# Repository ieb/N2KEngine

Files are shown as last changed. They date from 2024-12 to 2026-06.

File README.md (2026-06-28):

# N2K Engine Monitor

This monitors an engine, mostly temperatures and fuel, emitting suitable N2K messages. Targeting a Volvo Penta D2-40. Code and pcb are based on the interface board in https://github.com/ieb/EngineManagement, however this time the pcb is from scratch using a Atmel 328p directly to make the unit more robust. The original has been in service for 3 years with no problems seen, outlasting the Volvo Penta MDI unit, which failed 2x in < 4 years. Ok, the replacement was based on relays following the Perkins schematic for the same engine, so not really hard to do.

# PCB

Single board. If using a 328p chip you will need to flash the bootloader. See programBootLoader for details. 

## 328p based board 

<div>
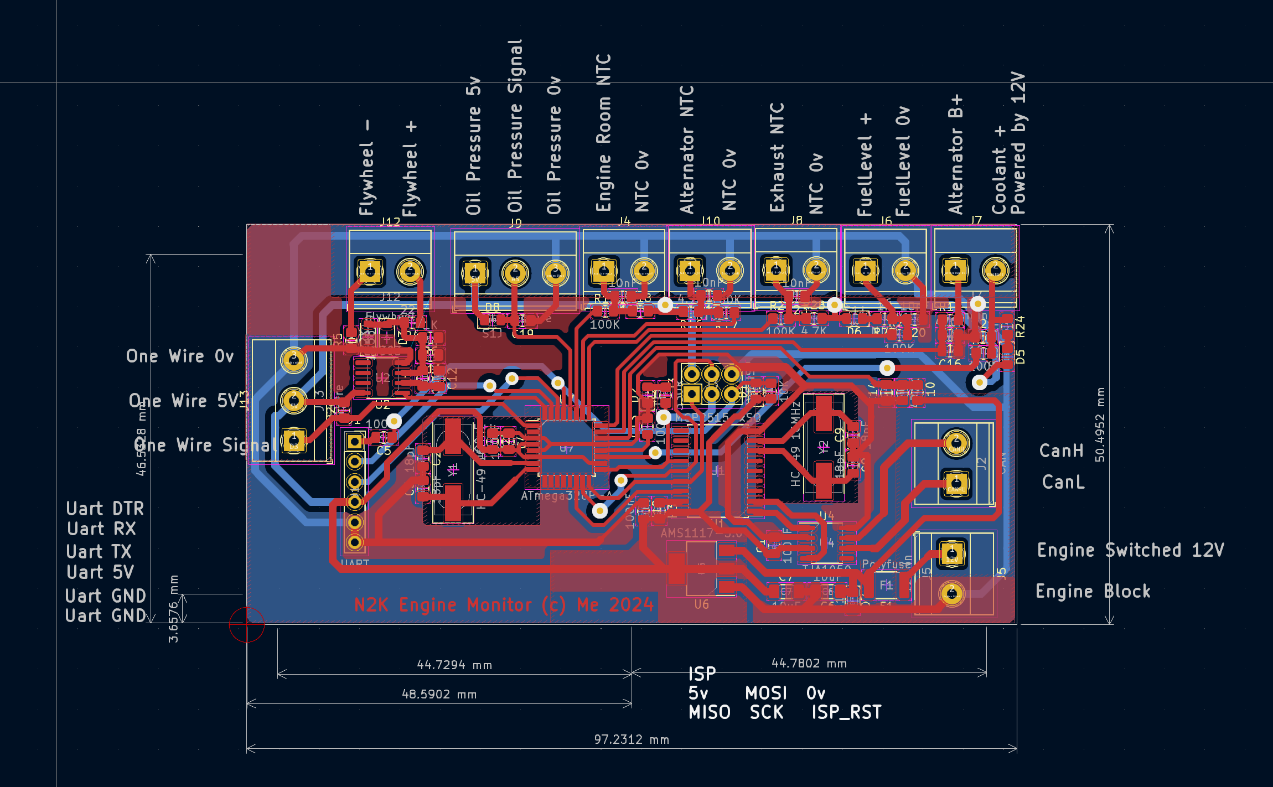
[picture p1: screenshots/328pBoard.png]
board

</div>

## Attiny3226 Board, 12bit ADCs and better RPM accuracy

<div>
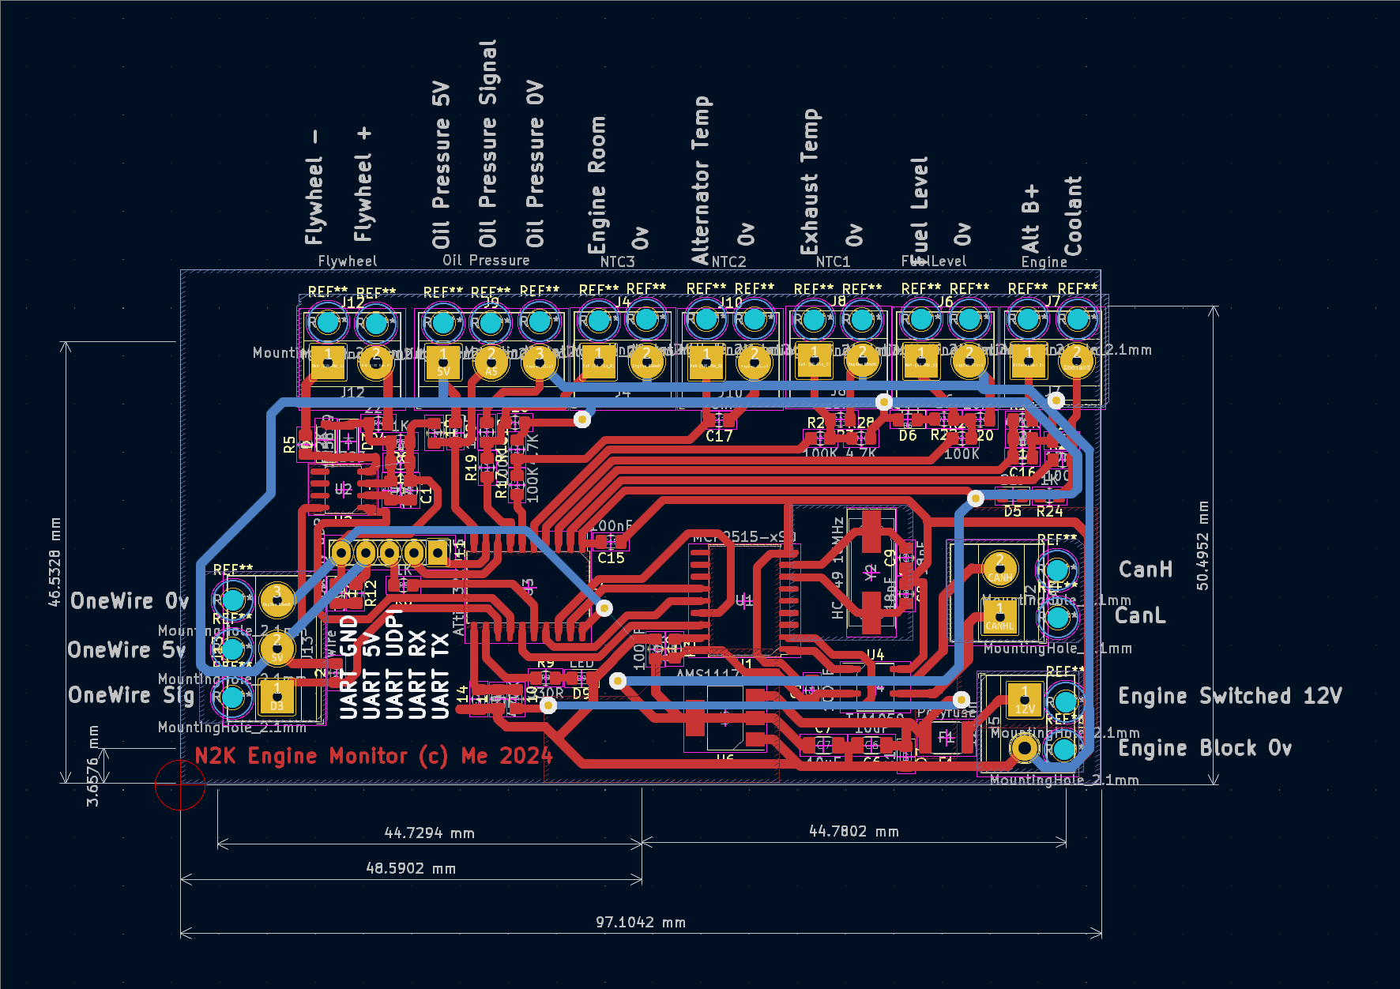
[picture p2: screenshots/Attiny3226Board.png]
board

</div>

# Setup

Setup starting with a new board, this is for 3226 which the preferred board.

* Test the board supply to check power consumption, should be about 30mA at both 5v and 12v.
* Connect up a UDPI programmer, and serial monitor.
* Burn Fuses, and tune the internal clock on the 3226, see tuning3226/README.md
* Upload the code.
* Connect a CAN bus with 1 other device.
* Verify CAN messages are sent and received (menu item d)
* Measure and set the supply voltage to the chip after powering with 12v. (menu item V)
* Check the Sensor diagnostics (menu item D, and M), might need to connect some NTC sensors and fake up flywheel source.
* Set the engine hours to match the existing board.
* Install the board

## Connection notes

* The GND connection must be made to the engine block (star pattern) to avoid GND voltage differences when the anternator is charging. Do not GND on the battery as that will result in dips in the coolant temperature of 5C or more. The battery voltage will include the GND drop on the charging line.

* The exhaust NCT should be connected to a part of the wet exhaust with good thermal connection to the inside of the exhaust. Do not connect to the elbow on the engine as this could result in false alarms when starting a warm engine. The trigger level is 45C or an 8C every 30s rise. Typically an exaust in UK waters on a D2-40 rests at 34-37C and rises rapidly should raw water fail.

## Changes from original build 4 years ago

* All components SMD, no draughtboards or modules with pin headers to fail.
* Switched from a LM385 to a LMV393 for the flywheel pulse generator as all I need is a clean square wave to count the pulses. (actually I miss ordered 10 LMV393's and then switched over).
* Changed to a 16MHz crystal on the MCP2515 since this is what the 328p is using. Perhaps 1 crystal would work for both, but probably not.

# Memory usage

after reducing memory requirements (580 used before), varies up an down a bit with debug.

attiny3226

    RAM:   [==        ]  20.1% (used 619 bytes from 3072 bytes)
    Flash: [========  ]  81.1% (used 26579 bytes from 32768 bytes)
NB, no malloc in use in code.
Over 77% Flash usag pio inspect no longer works, however removing One wire code may give enough space for debug symbols to allow inspect to work

# Status bits.

The status bits in PGN 127489 are set to indicate an alarm condition.

Alarm set levels and alarm clear levels are in enginesensors.h

WHen an alarm condition is set if the check engine, maintenance or emergency stop bits are set, they are not
cleared when the alarm clears. Generally advisable to stop the engine and check.

Emergency stop will be set when temperatures are too high. Best to stop the engine before damage occurs.

Over Temperature status 1 bit 1 set when over temperature is suspected including coolant (> 97C), exhaust > 45C, alternator > 110C, engine room > 70C. Will also set check engine and engine emergency shutdown alarms.

Low oil pressure alarm is set when oil pressure is < 10psi.

If sensors fail then engine comms alarm is set.

Water flow alarm uses the wet exhaust silencer probe as a proxy for raw water flow. The probe is mounted on the silencer body, which is in direct contact with the wet exhaust but thermally isolated from the engine block and heat exchanger — so silencer temperature reflects exhaust gas vs raw water flow only, and is not biased by block temperature on a warm restart. Two independent triggers, both gated on engine running, past the start-up grace period, and not stopping:

* Absolute over-temp: exhaust > 45C. WATER_FLOW and CHECK_ENGINE are set on the first sample; EMERGENCY_STOP is held off until the condition has persisted for 5s so a single noisy ADC sample cannot trip it.
* Rate-of-rise: exhaust climbs more than 8C in any 30s window once past the 35C baseline. This catches a flow failure before the absolute threshold (the 21-Jun-2026 incident showed a +9C rise in the first 30s while still well below 45C).

A coolant-vs-exhaust convergence check was previously included but removed: on a warm restart the silencer takes several minutes to thermalize while coolant is already at operating temperature, producing a coolant–exhaust gap that approaches the trip margin under entirely healthy conditions.

The alarm clears only once exhaust drops below 38C (widened from 40C) to avoid chatter on a cooling elbow.

Charge indicator alarm is set when the alternator voltage is < 12.8V

Engine shutdown alarm will be set when the engine is shutting down.

Other alarms are not set at this time.

# Building and Uploading

## Attiny3226 based board

Use UDPI. I use the old, slow and slightly buggy jtag2udpi programmer loaded onto an Uno. I use https://github.com/ieb/jtag2updi forked just in case. After programming the Uno needs a 10uF cap between reset and ground to prevent a reset on the Uno when programming starts.  The UDPI output is on Digital Pin 6 and connects via a 4K7 Resistor to the UDPI pin on the Attiny3226. The target board should be powered separately, and the serial monitor can remain attached while programming. Do not power the board using both a serial converter and the 12v power supply as this will cause the serial port to draw too much USB current and be shutdown. Programing setup is in platformio.ini. Before programming a fresh chip, set the fuses to set the CPU Frequency.

Fresh boards also need to go through a runing process , see tuning3226/

Obviously edit platform.ini with the correct serial ports for upload and monitoring.

    pio run -e attiny3226 -t fuses

Then upload code with an upload command. Fuses only need to be set once per chip.

    pio run -e attiny3226 -t upload

To monitor 

    pio device monitor

### Clock Tuning 3226

The 3226 board uses an internal oscilator due to lack of pins and so it needs tuning from a board with a quartz crystal as per https://github.com/SpenceKonde/megaTinyCore/blob/master/megaavr/extras/Ref_Tuning.md. The Tuning source needs to be https://github.com/SpenceKonde/megaTinyCore/tree/master/megaavr/libraries/megaTinyCore/examples/TuningSource uploaded onto a Uno or any 328p with pin 9 available. The UNO must have an real crystal not a resonator.  The tuning code is https://github.com/SpenceKonde/megaTinyCore/tree/master/megaavr/libraries/megaTinyCore/examples/megaTinyTuner, but for these boards must be modified to use PB1 as the timing pin since this is exposed directly. (Oil pressure sense).  Copies of both of these are in tuning as they needed minor modifications.

## 328p based board

Can be built on any 328p suitably wired, however to build using the pcb design first flash a bootloader, see [programBootLoader/README.md] for details, then come back here.

Having flashed with the urbootloader connect a serial adapter configured for 5V to the serial header pins, adjust platform.ini to reflect the serial port and run

    pio run -t upload

to monitor

    pio device monitor

Do not attempt to power the board both on the 12v line and through the serial port 5v at the same time. This will probably shutdown the USB port on your laptop (or worse produce some smoke) Monitoring over serial can be done provided only GND, TX and RX are attached. Ie no power from the serial adapter.

# LM393 RPM to pulses

Critical that this chip as a 100nF decoupling capacitor. Without it it will generate pulses from power supply noise with the inputs shorted together. See schematic. LTSpice models don't predict this behavior.

# Engine Events

Stores upto 29 events in EEPROM, with a 15s resolution and one of upto 255 types.
All the following PGNS have standard priorietary PGN format + a Function code byte.
The Manufactore code is 2046 and the Industry is Marine, ie 4.

# PGN Abuse

Since Raymarine instuments display only a asubset of PGNs, some are beeing abused to get critical temperatures avialable on the insturments.

* alternator temperature, critical for LiFePO4 charging, is sent as oil temperature in Dynamic Engine Parameters (PGN 127489)
* ehxhaust temperature, critical for raw water flow monitoring, is sent as transmission oil temperature in Dynamic Transmiossion Parameters (PGN 127493L)

# Temperature PGN 130312 non standard IDs

* Exhaust temperature is sent as ID 30
* Additional OneWire Temperature probes are sent as IDs 31-35 where present.

## PGN 65305L

Standard  Packet proprietary, 8 bytes

| Field | Length | Value     | Description            |
|-----------------------------------------------------|
| 1     | 11 bits| 2046      | Manufacturer code      |
| 2     | 2 bits |           | Rserved                |
| 3     | 3 bits | 4 (0b100) | Industry Code          |
| 4     | 8 bits |           | Requst Function Number |
| 5     | 5 bytes|           | reserved/payload       |

|  Function | Description | Valid PGN | Response |
|---|---|---|---|
| 11 | Get events | 65305L | Events PGN 130817L Functon 12 |
| 12 | Get events response | 130817L | List of events |
| 13 | Clear events | 65305L | ACK PGN 65305L Functon 14, no payload |
| 14 | Clear events ACK | 65305L | Ack clear events, no payload |

## PGN 130817L

| Field | Length | Value | Description |
|---|---|---|---|
| 1 | 11 bits| 2046 | Manufacturer code |
| 2 | 2 bits | | Rserved |
| 3 | 3 bits | 4 (0b100) | Industry Code |
| 4 | 8 bits | | Requst Function Number |

## Function 12

| Field | Length  | Value | Description | 
|---|---|---|---|
| 4 | 1 byte  | uint8_t | Number of events |
| 5+(n*4) | 1 byte  | uint8_t | Event ID |
| 6+(n*4) | 3 bytes | 3Byte UDouble 0.001 | Engine Hours of event (15s resolution) |

| Event ID | Meaning |
|---|---|
| 0 | Current engine hours, no event |
| 1 | Engine Stop |
| 2 | Low Oil Pressure |
| 3 | High Coolant Temperature |
| 4 | High Exhaust Temperature |
| 5 | High Alternator Temperature |
| 6 | High Engine Room Temperature |

# Todo

* [x] build board.
* [x] Flash bootloader and test
* [x] Port code from original
* [x] Allow for 16MHz MCP2515 oscillator, current library uses 8MHz.
* [x] Handle when engine not running, now that device is powered from CanBus
* [x] Reduce memory requirements in EngineSensorts and bind measurements to messages.
* [x] PR SmallNMEA2000 with changes
* [x] Test and Calibrate NTCs
* [x] Test and Calibrate Coolant and fuel
* [x] Test On N2K Bus
* [x] Implement 1 wire
* [x] Allow Engine Hours to be set via serial
* [x] Improve status and diagnostics to include n2k traffic
* [x] Implement status alarms
* [x] Consider swapping NTC4 for a oil pressure sensor if it can be accommodated.
* [x] Power from Engine supply since oil pressure sensors use > 10mA typically. This means fuel levels and temperature will only be available with engine controls turned on.
* [x] Check voltage calibration, some doubt over digtal multi meter accuracy used previously - verified against a ADS1115 to be accurate
* [x] Add firmware version, shows on the help, press h when connected over serial.
* [x] Create a attiny3226 based board, with 12bit ADCs for better resolution on the voltages.
* [x] Calibrate CPU clock
* [x] Verify RPM accuracy (measured at +- 0.2% relative to calibrated 16Mhz crystal)
* [x] Verify NTC and other ADC readings.
* [x] Install onboard
* [x] Implement event storage
* [x] Implement PGN proprietary messages to query engine events.
* [x] Update schematic to improve ADC stability when charging main LiFePO4s
* [x] Fix OneWire on Attiny3226 (see lib/vportonewire)
* [x] Fix event streaming to contain the right number of events including current hours.
* [x] Read stop button, on PC0. This will go to 12V when the solenois is powered.
* [x] Lowered alternator low voltage alarm to 12.2v and added window for overheat to combat high noise levels on the coolant sensor.
* [x] Added window period for all alarms to avoid 1 reading triggering alarm condition, set a 5s. 
* [x] Fixed (hopefully, need to test on engine) noise in in Engine Coolant readings, due to 12v ripple.
* [ ] Check the divders, which we specked at 100K/47K which could be too large for the ADC capacitance.

# Could do... but probably will not

The board currently runs of switched engine power, so to read fuel tank and batteries the engine has to be turned on. This is good, since power consumption becomes irrelevant although its typically < 80mA. I could optimize so that the board could be powered from the Can bus, but probably wont. Better to have it off when 
not relevant.. eg when sailing.

# New Board check list

* Oil sensor with pot
* NTCs, set Vdd then 10K == 25C, 22K == 8C, Check thermstor against room temp and body temp.
* Check Fuel 190R == full 0R == empty, linear, 120R == 120/190 = 63%  47/190 == 24
* Check AltV by connecting to suppy V
* Check Coolant, Supply -> 1K top. 22R == 120C, 120R == 60+10*(134-120)/(134-97) = 63
* Check RPM with a 1KHz signal
* Check oneWire
* Check CAN and engine events are responding, verifies can read and write.

# Engine overheat data from 21 July 2026.

Had been motoring for about 45m, 2.2K rpm all stable.

* 10:08:45 Coolant 87C, Exhaust 38.4C, Engine Room 57. raw water hose detaches, sudden drop in Engine Room temperature due to water spraying engine bay. Exhaust note changed.
* 10:09:00 Coolant 90C, Exhaust 40.2, Engine 50C
* 10:09:15 Coolant 92.7C, Exhaust 47.1, Engine 49.4C
* 10:09:30 Coolant 95.2C, Exhaust 51.9, Engine 48.6C  <<< Should have alarmed here.
* 10:09:45 Coolant 97.4C, Exhaust 57.9, Engine 47.3C
* 10:09:55 Coolant 98.3C, Exhaust 62.6, Engine 47.1C  engine was turned off before overheat.

Exhaust elbow temperature rises rapidly 22C over 1m vs 8C over the same period for the engine coolant temperature, although at the time no raw water alarm sounded as the limit was set at 80C and there was no display showing exhaust temperature.

Exhaust elbow temperature seems to be a strong indicator of water flow once the engine is running at temperature.

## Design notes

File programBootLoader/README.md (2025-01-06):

# Program an Arduino UNO with Arduino ISP 

Only the 328p based board needs a bootloader. The Attiny board is programmed over UDPI with no bootloader, see main readme.

This will program a 328p with a urboot bootloader from https://github.com/MCUdude/MiniCore where previously there was none. Once the bootloader is used, standard programming over UART can be used. Fuses are also set here, see platform.ini here for more details.

## Connect

* Uno 10uF between RST and GND to stop it reseting while programming
* Uno -> Target
* 0V -> 0V
* 5V -> 5V
* D10 -> ISP Reset
* D11 -> MOSI
* D12 -> MISO
* D13 -> SCK

run

    pio run -e fuses_bootloader_uno_isp -t bootloader

output should end with....

        ....
        avrdude: verifying ...
        avrdude: 1 bytes of lock verified

        avrdude: safemode: lfuse reads as F7
        avrdude: safemode: hfuse reads as D6
        avrdude: safemode: efuse reads as FC
        avrdude: safemode: Fuses OK (E:FC, H:D6, L:F7)

        avrdude done.  Thank you.

        =========================================================================== [SUCCESS] Took 3.98 seconds ===========================================================================

        Environment               Status    Duration
        ------------------------  --------  ------------
        fuses_bootloader_uno_isp  SUCCESS   00:00:03.983
        =========================================================================== 1 succeeded in 00:00:03.983 ===========================================================================

Then the LED on SCK should be flashing. The default program is blink.

Now the board can be programmed over UART as normal. The bootloader is urboot

# Errors

If avrdude reports

    avrdude: stk500_recv(): programmer is not responding

Then check the 10uF cap is connected properly (or the wrong port is used)

If avrdude reports

    avrdude: Device signature = 0x000000
    avrdude: Yikes!  Invalid device signature.
             Double check connections and try again, or use -F to override
             this check.

Try swapping MOSI and MISO

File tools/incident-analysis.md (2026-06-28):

# Engine cooling-failure analysis — May & June 2026 incidents

Analysis of two raw-water-flow / overheat events captured by the
`nmeabridgeapp` per-day binary history, used to validate the water-flow
alarm-logic changes in `lib/enginesensors/`.

Source data: `nmeabridgeapp/datasets/engine-YYYY-MM-DD.bin` (one record per
second, format documented in `nmeabridgeapp/doc/history-log-format.md` and
`EngineProtocol.kt`).

Decoder: `tools/engine_log.py` — pure-Python, stdlib only. Subcommands:

```
python3 tools/engine_log.py summary <files>           # per-run statistics
python3 tools/engine_log.py csv     <files>           # per-second CSV
python3 tools/engine_log.py trace   --peak coolant <files>   # window around peak
```

## Healthy baseline (D2-40, all good runs across 30–31 May, 20–21 Jun 2026)

| metric | typical warmed-up range |
|---|---|
| coolant | 80 – 92 C |
| **exhaust elbow** | **31 – 39 C** (mean 34–36 C) |
| coolant – exhaust gap (rpm > 1200) | **45 – 55 C** (means 48–52 C) |
| alternator | 60 – 85 C |
| engine room | 40 – 65 C |
| alternator V / battery V | 13.7–14.5 / 13.5–14.0 |

Confirms the firmware comment that "normal water flow on the elbow is 37C".
The alarm constants — 45 C absolute trip, 35 C rise-anchor baseline,
8 C rise-in-30 s — are all comfortably outside healthy variation.

## Why no coolant-convergence trigger

An earlier version of the firmware included a coolant-vs-exhaust convergence
trigger (fire if `coolant - exhaust < 30 C` once coolant > 70 C). It was
removed after the warm-restart sequence on run 2 of 21 Jun was inspected:
the silencer (where the exhaust probe is mounted) is thermally isolated from
the engine block, so on a warm restart the block is at ~85 C while the
silencer has cooled toward ambient. At 09:30:45 — engine at 1380 rpm, all
healthy — coolant was 82.0 C and exhaust 51.4 C: gap 30.6 C, **0.5 C from
tripping the convergence alarm**. Exhaust then fell monotonically for ~5 min
as raw water cooled the silencer faster than exhaust gas heated it, before
diverging into the normal ~50 C steady-state gap. Convergence is therefore
a false-positive risk on every warm restart, while contributing no
detectable lead time on either captured failure mode (it does not fire at
all on the sudden-detachment case and is the *last* of the three triggers
to fire on the slow-degradation case). Removed.

## Note on dating

The README incident headed *"21 July 2026"* is in fact recorded in
`engine-2026-06-21.bin` at 09:09 UTC (10:09 BST). There is no
`engine-2026-06-22.bin`. Both this document and the README's narrative
refer to the same 21 June 2026 event.

## Incident A — 2026-05-31, slow flow degradation

Run starts 10:03:35 UTC at ~1500 rpm, coolant ~62 C from a previous warmup.
The exhaust elbow climbs roughly linearly from start: about +1 C every
5 s once past 30 C, i.e. ~12 C/min — well above the new rate-of-rise
threshold (8 C in 30 s).

| time (UTC) | rpm | coolant | exhaust | gap | event |
|---|---|---|---|---|---|
| 10:03:44 | 1348 | 64.0 | 27.1 | 36.9 | start, gap normal |
| 10:04:34 | 1522 | 66.1 | 31.3 | 34.8 | exhaust climbing fast for a cold engine |
| 10:05:54 | 1664 | 79.6 | 45.7 | 33.9 | exhaust > 45 C — abs trip |
| 10:06:09 | 1675 | 78.7 | 50.5 | 28.2 | gap < 30 C — convergence trip |
| 10:07:39 | 1333 | 96.6 | 66.2 | 30.4 | coolant > 95 C |
| 10:08:39 | 1341 | 91.6 | 74.1 | **17.5** | gap collapsed |
| 10:09:11 | 1350 | **101.2** | 77.5 | 23.7 | peak coolant |
| 10:09:14 | 759 | 98.2 | 78.0 | 20.2 | rpm cut to idle |
| 10:09:24 | 767 | 99.1 | 78.4 | 20.7 | CHECK_ENGINE / MAINTENANCE asserted |
| 10:09:39 | 764 | 99.1 | 79.7 | 19.4 | OVERTEMP asserted |
| 10:09:54 | 769 | 100.7 | 80.0 | 20.7 | last sample, engine off shortly |

When the new alarm logic would trip (replayed against the data):

| trigger | first fires at | lead time vs OVERTEMP (10:09:39) |
|---|---|---|
| rate-of-rise (8 C / 30 s) | ~10:05:30 (cool 73 C) | **~4 min earlier** |
| absolute > 45 C | 10:05:54 (cool 80 C) | ~3 min 45 s earlier |

The old code (45 C absolute, no persistence) also tripped at 10:05:54, but
OVERTEMP was the only bit eventually set in the historical record — and
that didn't happen until 4 minutes later. **This is the failure mode where
the new rate-of-rise trigger adds real, measurable detection time.**

## Incident B — 2026-06-21, sudden hose detachment

Warm restart at 09:30 BST, stable cruise at ~2200 rpm. Coolant locks at
86–87 C, exhaust at 37–38 C, gap at ~49 C for ~9 minutes — textbook
healthy operation. Then a hose detachment causes the failure described in
README §"Engine overheat data from 21 July 2026" (date typo in README).

| time (UTC) | rpm | coolant | exhaust | gap | event |
|---|---|---|---|---|---|
| 09:08:45 | 2235 | 87.1 | 38.4 | 48.7 | normal |
| 09:09:00 | 2235 | 90.0 | 40.2 | 49.8 | hose detaches; exhaust climbing |
| 09:09:15 | 1480 | 92.7 | 47.1 | 45.6 | exhaust > 45 C; skipper throttles back |
| 09:09:30 | 1632 | 95.8 | 51.9 | 43.9 | coolant > 95 C |
| 09:09:45 | 1480 | 97.6 | 57.9 | 39.7 | — |
| 09:09:55 | 833 | 98.3 | 62.6 | 35.7 | engine going to idle / shutdown |
| 09:09:58 | 833 | — | 62.6 | — | coolant signal lost (engine off) |

Exhaust rose **+24 C in 55 s** (~26 C/min). No alarm bits were set by
the firmware in service that day — the only status1/2 flag seen on 21 Jun
across the whole file was `CHARGE_INDICATOR` from an unrelated earlier
run. Consistent with the README: the in-service threshold was 80 C, peak
exhaust was 62.6 C, no alarm fired and no display showed exhaust temp.

When the new alarm logic would trip:

| trigger | first fires at | notes |
|---|---|---|
| rate-of-rise (8 C / 30 s) | 09:09:15 (+8.7 C since 09:08:45) | tied with abs |
| absolute > 45 C | 09:09:15 (47.1 C) | tied with rate |

Rate-of-rise and absolute fire **simultaneously** here. The value of the
new logic in this incident is that it actually fires (the in-service
80 C threshold did not), with the absolute + 5 s persistence reaching
EMERGENCY_STOP at ~09:09:20.

## Conclusions

1. Healthy baseline data validates the alarm constants — they sit
   well outside normal-operation variation in both warmed-up cruise and
   warmup transients.
2. The May incident (slow degradation) is where the rate-of-rise trigger
   adds several minutes of detection time over an absolute-only check.
3. The June incident (sudden detachment) is caught at the same instant
   by absolute and rate-of-rise. The improvement here is over the
   original 80 C threshold that was actually in service, which never
   tripped.
4. The 5 s EMERGENCY_STOP persistence and engine-running gate are
   defence-in-depth against bad samples and hot-soak / hot-restart false
   positives. Neither incident exhibited those failure modes, but the
   cost of including them is negligible.
5. A coolant-vs-exhaust convergence trigger was considered and removed:
   the silencer (where the exhaust probe is mounted) is thermally
   isolated from the block, so on a warm restart the coolant–exhaust
   gap shrinks to within ~0.5 C of the trip margin under entirely
   healthy conditions before re-diverging. See the warm-restart section
   above.

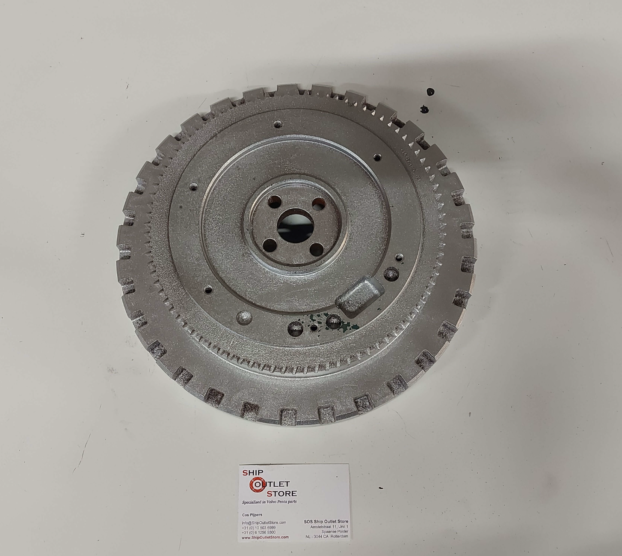
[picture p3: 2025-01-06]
screenshots/flywheel-D2-40.png

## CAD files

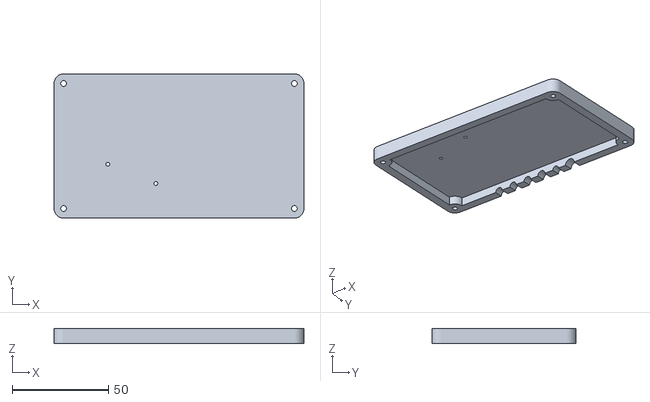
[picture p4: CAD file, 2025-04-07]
pcb/lid.stl
130.0 x 75.0 x 8.00

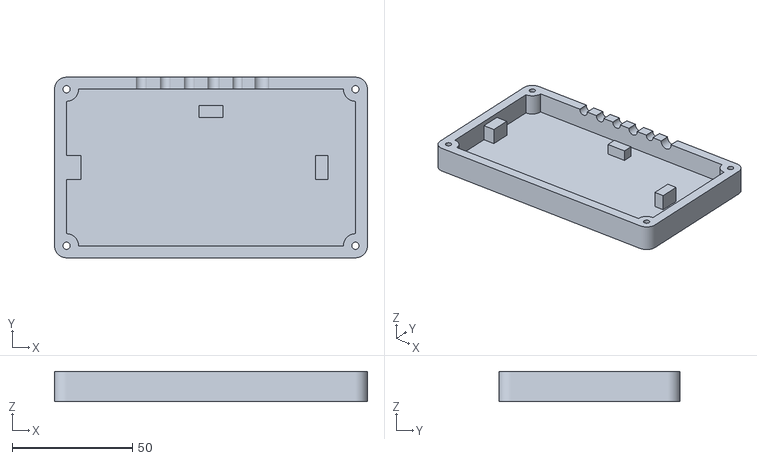
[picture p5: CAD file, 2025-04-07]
pcb/case.stl
130.0 x 75.0 x 12.5

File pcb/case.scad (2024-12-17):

$fn=100;



module cables() {
  translate([0,0,0]){

    // can cable
    translate([100,18,3]) 
    rotate([0,90,0]) {
    cylinder(d=6, h=50);
        translate([-2.7,0,15])
        cube([6,6,15], center=true);
    }
     

    // power
    translate([82,52,3])
    rotate([-90,0,0]) {
    cylinder(d=4, h=50);
                translate([0,-3,15])
        cube([4,5.4,15], center=true);

    }

    //  ntc
    translate([54,52,3])
    rotate([-90,0,0]) {
    cylinder(d=5, h=50);
                translate([0,-3,15])
        cube([5,5,15], center=true);
    }

    //
    translate([32,52,3])
    rotate([-90,0,0]) {
    cylinder(d=4.5, h=50);
                translate([0,-3.3,15])
        cube([4.5,4.5,15], center=true);
    }

    //
    translate([22,52,3])
    rotate([-90,0,0]) {
    cylinder(d=4.5, h=50);
                translate([0,-3.3,15])
        cube([4.5,4.5,15], center=true);
    }

    //
    translate([11,52,3])
    rotate([-90,0,0]) {
    cylinder(d=4.5, h=50);
                translate([0,-3.3,15])
        cube([4.5,4.5,15], center=true);
    }
    }
}

module board() {
    
        translate([11,3,0]) 
        union() {
            cube([97,52,4]);
           // connectors
            color("blue") {
                // serial just for height
                translate([12,8,0])
                cube([3,22,11]);
                
                cables();

                
                // LED
                translate([51,31,0])
                            cylinder(h=25,d=2);


            }


        };
}



module lid(w=130,d=75,h=8,t=5) {
   difference() {
        translate([w/2,d/2-3,12]) 
      difference() {
        union() {
            difference() {
                union() {
                    cube([w-t*2,d,h], center=true);
                    cube([w,d-t*2,h], center=true);
                    translate([w/2-t,d/2-t,0])
                    cylinder(r=t,h=h, center=true);
                    translate([-(w/2-t),d/2-t,0])
                    cylinder(r=t,h=h, center=true);
                    translate([-(w/2-t),-(d/2-t),0])
                    cylinder(r=t,h=h, center=true);
                    translate([w/2-t,-(d/2-t),0])
                    cylinder(r=t,h=h, center=true);
                    

                }
                // inside
                translate([0,0,-8])
                    cube([w-t*2,d-t*2,h+t*2], center=true);
            }
            
            

            
            // fxings
            translate([w/2-t,d/2-t,0])
                    cylinder(r=5,h=h, center=true);
            translate([-(w/2-t),d/2-t,0])
                    cylinder(r=5,h=h, center=true);
            translate([-(w/2-t),-(d/2-t),0])
                    cylinder(r=5,h=h, center=true);
                    translate([w/2-t,-(d/2-t),0])
                    cylinder(r=5,h=h, center=true);
        }
        
            translate([w/2-t,d/2-t,0])
                    cylinder(d=3,h=h+10, center=true);
            translate([-(w/2-t),d/2-t,0])
                    cylinder(d=3,h=h+10, center=true);
            translate([-(w/2-t),-(d/2-t),0])
                    cylinder(d=3,h=h+10, center=true);
                    translate([w/2-t,-(d/2-t),0])
                    cylinder(d=3,h=h+10, center=true);
    }
    



        // led
  
        board();

    }
    
    
        translate([11,3,0]) {
        // can cable
    translate([100,18,3]) 
    rotate([0,90,0]) {
        difference() {
        translate([-2.7,0,16.5])
        cube([6,5.8,5], center=true);
    cylinder(d=6, h=50);
        }
    }
     

    // power
    translate([82,52,3])
    rotate([-90,0,0]) {
        difference() {
                translate([0,-3,14.4])
        cube([3.8,5.4,t], center=true);
    cylinder(d=4, h=50);
        }

    }

    //  ntc
    translate([54,52,3])
    rotate([-90,0,0]) {
        difference() {
                translate([0,-3,14.4])
        cube([4.8,5,5], center=true);
    cylinder(d=5, h=50);
        }
    }

    //
    translate([32,52,3])
    rotate([-90,0,0]) {
        difference() {
                translate([0,-3.3,14.4])
        cube([4.3,4.5,5], center=true);
    cylinder(d=4.5, h=50);
        }
    }

    //
    translate([22,52,3])
    rotate([-90,0,0]) {
        difference() {
                translate([0,-3.3,14.4])
        cube([4.3,4.5,5], center=true);
    cylinder(d=4.5, h=50);
        }
    }

    //
    translate([11,52,3])
    rotate([-90,0,0]) {
        difference() {
                translate([0,-3.3,14.4])
        cube([4.3,4.5,5], center=true);
    cylinder(d=4.5, h=50);
         }
   }
    }

}

module case(w=130,d=75,h=12.5,t=5) {
   difference() {
   translate([w/2,d/2-3,2]) 
      difference() {
        union() {
            difference() {
                union() {
                    cube([w-t*2,d,h], center=true);
                    cube([w,d-t*2,h], center=true);
                    translate([w/2-t,d/2-t,0])
                    cylinder(r=t,h=h, center=true);
                    translate([-(w/2-t),d/2-t,0])
                    cylinder(r=t,h=h, center=true);
                    translate([-(w/2-t),-(d/2-t),0])
                    cylinder(r=t,h=h, center=true);
                    translate([w/2-t,-(d/2-t),0])
                    cylinder(r=t,h=h, center=true);
                    

                }
                // inside
                translate([0,0,t])
                    cube([w-t*2,d-t*2,h+t], center=true);
            }
            

            // fxings
            translate([w/2-t,d/2-t,0])
                    cylinder(r=5,h=h, center=true);
            translate([-(w/2-t),d/2-t,0])
                    cylinder(r=5,h=h, center=true);
            translate([-(w/2-t),-(d/2-t),0])
                    cylinder(r=5,h=h, center=true);
                    translate([w/2-t,-(d/2-t),0])
                    cylinder(r=5,h=h, center=true);
        }
        
        translate([w/2-t,d/2-t,0])
                cylinder(d=3,h=h+10, center=true);
        translate([-(w/2-t),d/2-t,0])
                cylinder(d=3,h=h+10, center=true);
        translate([-(w/2-t),-(d/2-t),0])
                cylinder(d=3,h=h+10, center=true);
        translate([w/2-t,-(d/2-t),0])
                cylinder(d=3,h=h+10, center=true);
    }
    board(); 
    }
}




/*
difference() {
    union() {
        //board();
        color("green") case();
        lid();
    }

   translate([0,0,0])
   cube([20,50,140], center=true);
}
*/



//board();
//color("green") case();
lid();

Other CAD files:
pcb/case2.scad

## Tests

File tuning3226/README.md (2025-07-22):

# Tuning Attiny3226 clock

This is required to get accurate RPM radings. The clock on the Attiny is stable and accurate once tuned.

## Process

In the parent directory burn the fuses to set the clock speed of the Attiny3226 to 16MHz

    cd ../
    vi platform.ini # to set the serial ports 
    pio run -e attiny3226 -t fuses

upload tuningSource to a Uno which will produce a 500Hz square wave on pin 9. The Uno must have a genuine crystal clock source, not a resonator.

    cd tuningSource
    pio run -e uno -t upload

Connect Uno pin 9 to PB1 (Oil pressure signal) on the board.

Upload megaTinyTuner and monitor the serial line to ensure check the process completes.

    cd megaTinyTuner
    pio run -e attiny3226 -t upload

Output from the attiny3226 will be something like the following possibly with different numbers.

    tuning with new sketch
    25:35:53:71:78:80
    tuning
    Dump of USERSIG after tuning
    25:35:53:71:78:80
    Tuning should now be complete.

Once tuned, the main program can be uploaded

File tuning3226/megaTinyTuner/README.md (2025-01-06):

# Mega Tiny Tuner

Copied from https://github.com/SpenceKonde/megaTinyCore/tree/master/megaavr/libraries/megaTinyCore/examples/megaTinyTuner to adjust for this board and make work with platformIO as used here.

NOte the source needs to be 500Hz with exactly 50% duty cycle so that the pulse width is exactly 1ms for both high and low pulses. Anything else wont work.

# Modifications

* Need to use a pin that is exposed, PB1 looks good as it is the Oil Pressure sensor sense pin, with only a 10nF cap to ground. There is a protective diode to +5V, but nothing else. Hopefully the 10nF will not impact the rise time of the pulse.

* FORCE_PIN PA6 is connected to Fuel level which is normally pulled high and can be pulled low if required. No change here.

* Serial debug output modified to give clearer feedback .... wasnt sure it worked first time. 

* added platformio.ini to fit with my dev flow and programers.

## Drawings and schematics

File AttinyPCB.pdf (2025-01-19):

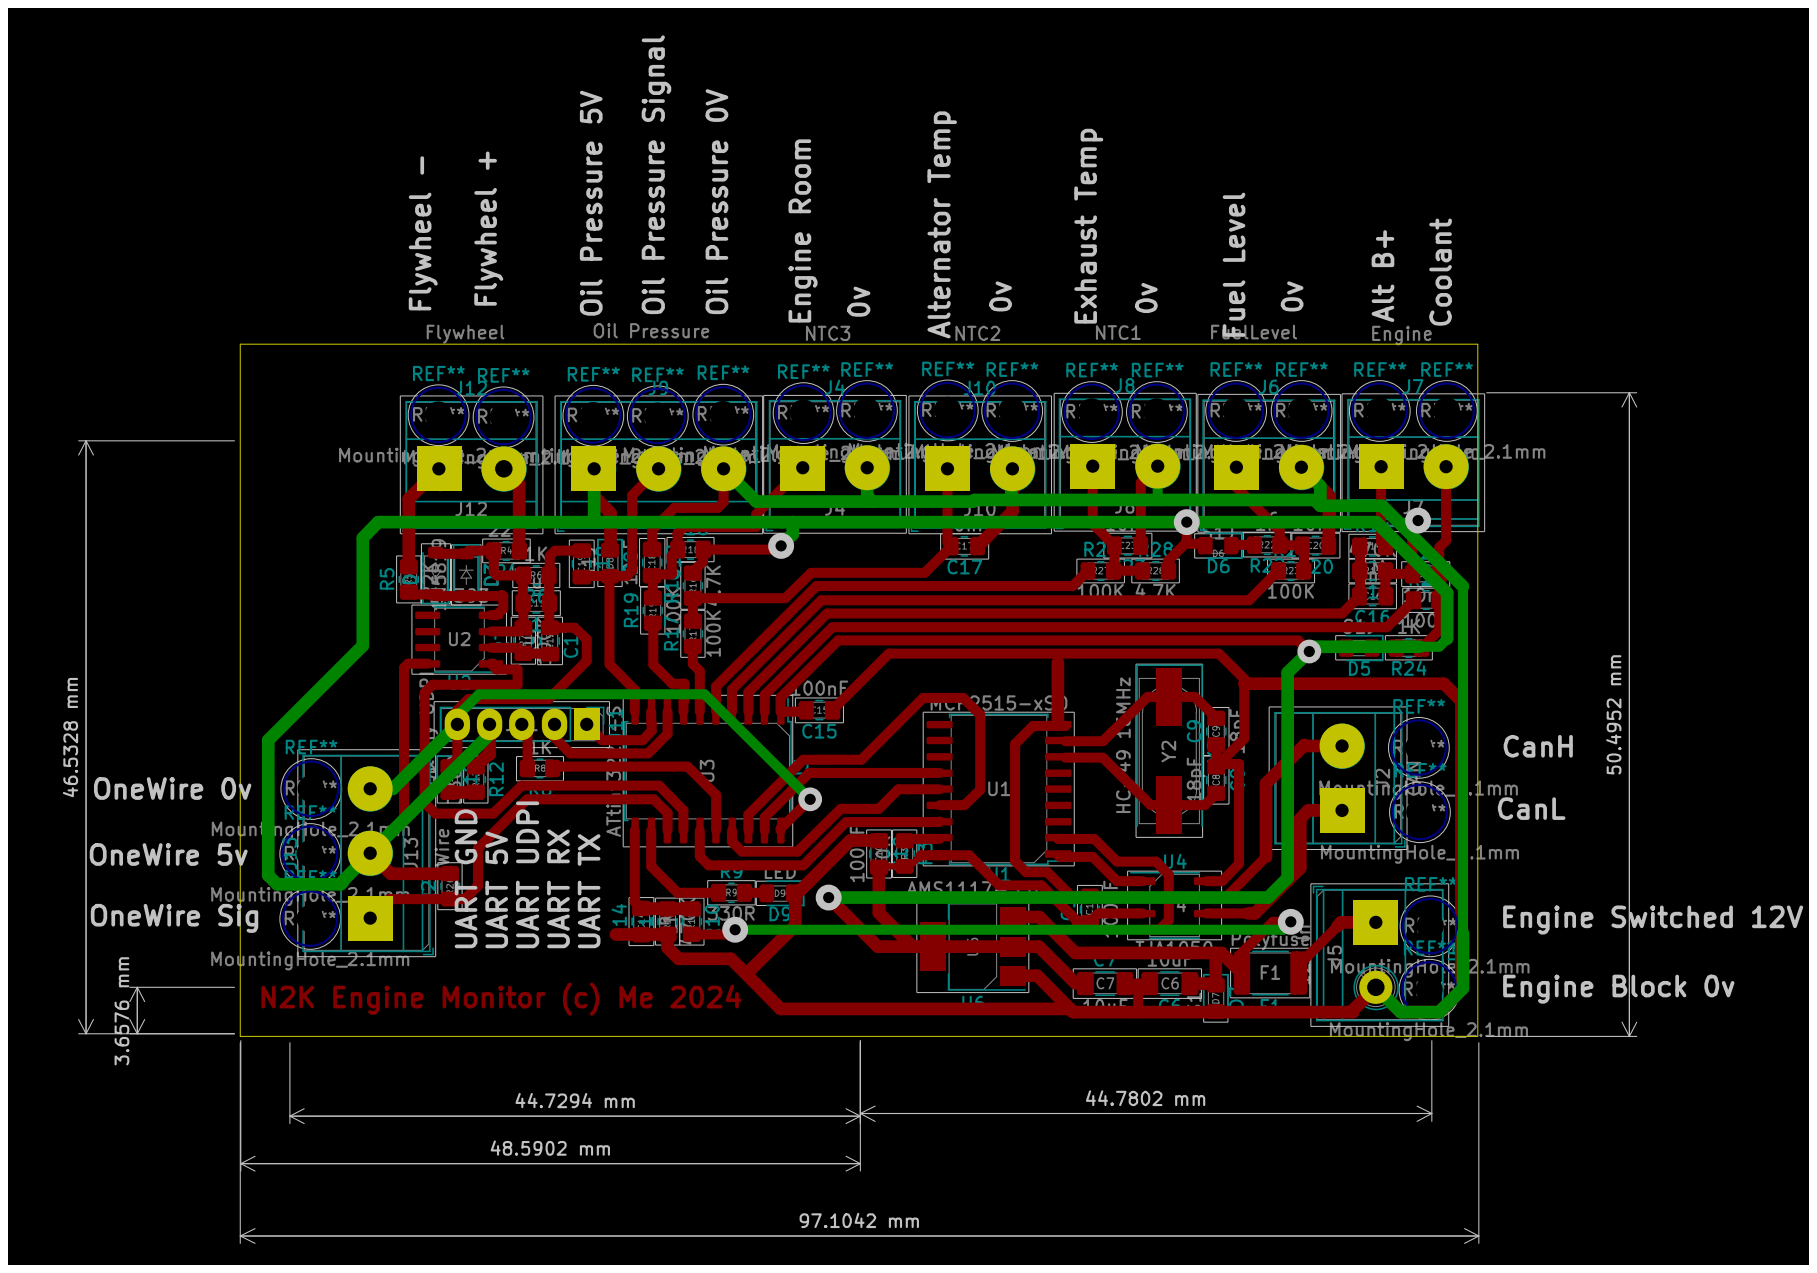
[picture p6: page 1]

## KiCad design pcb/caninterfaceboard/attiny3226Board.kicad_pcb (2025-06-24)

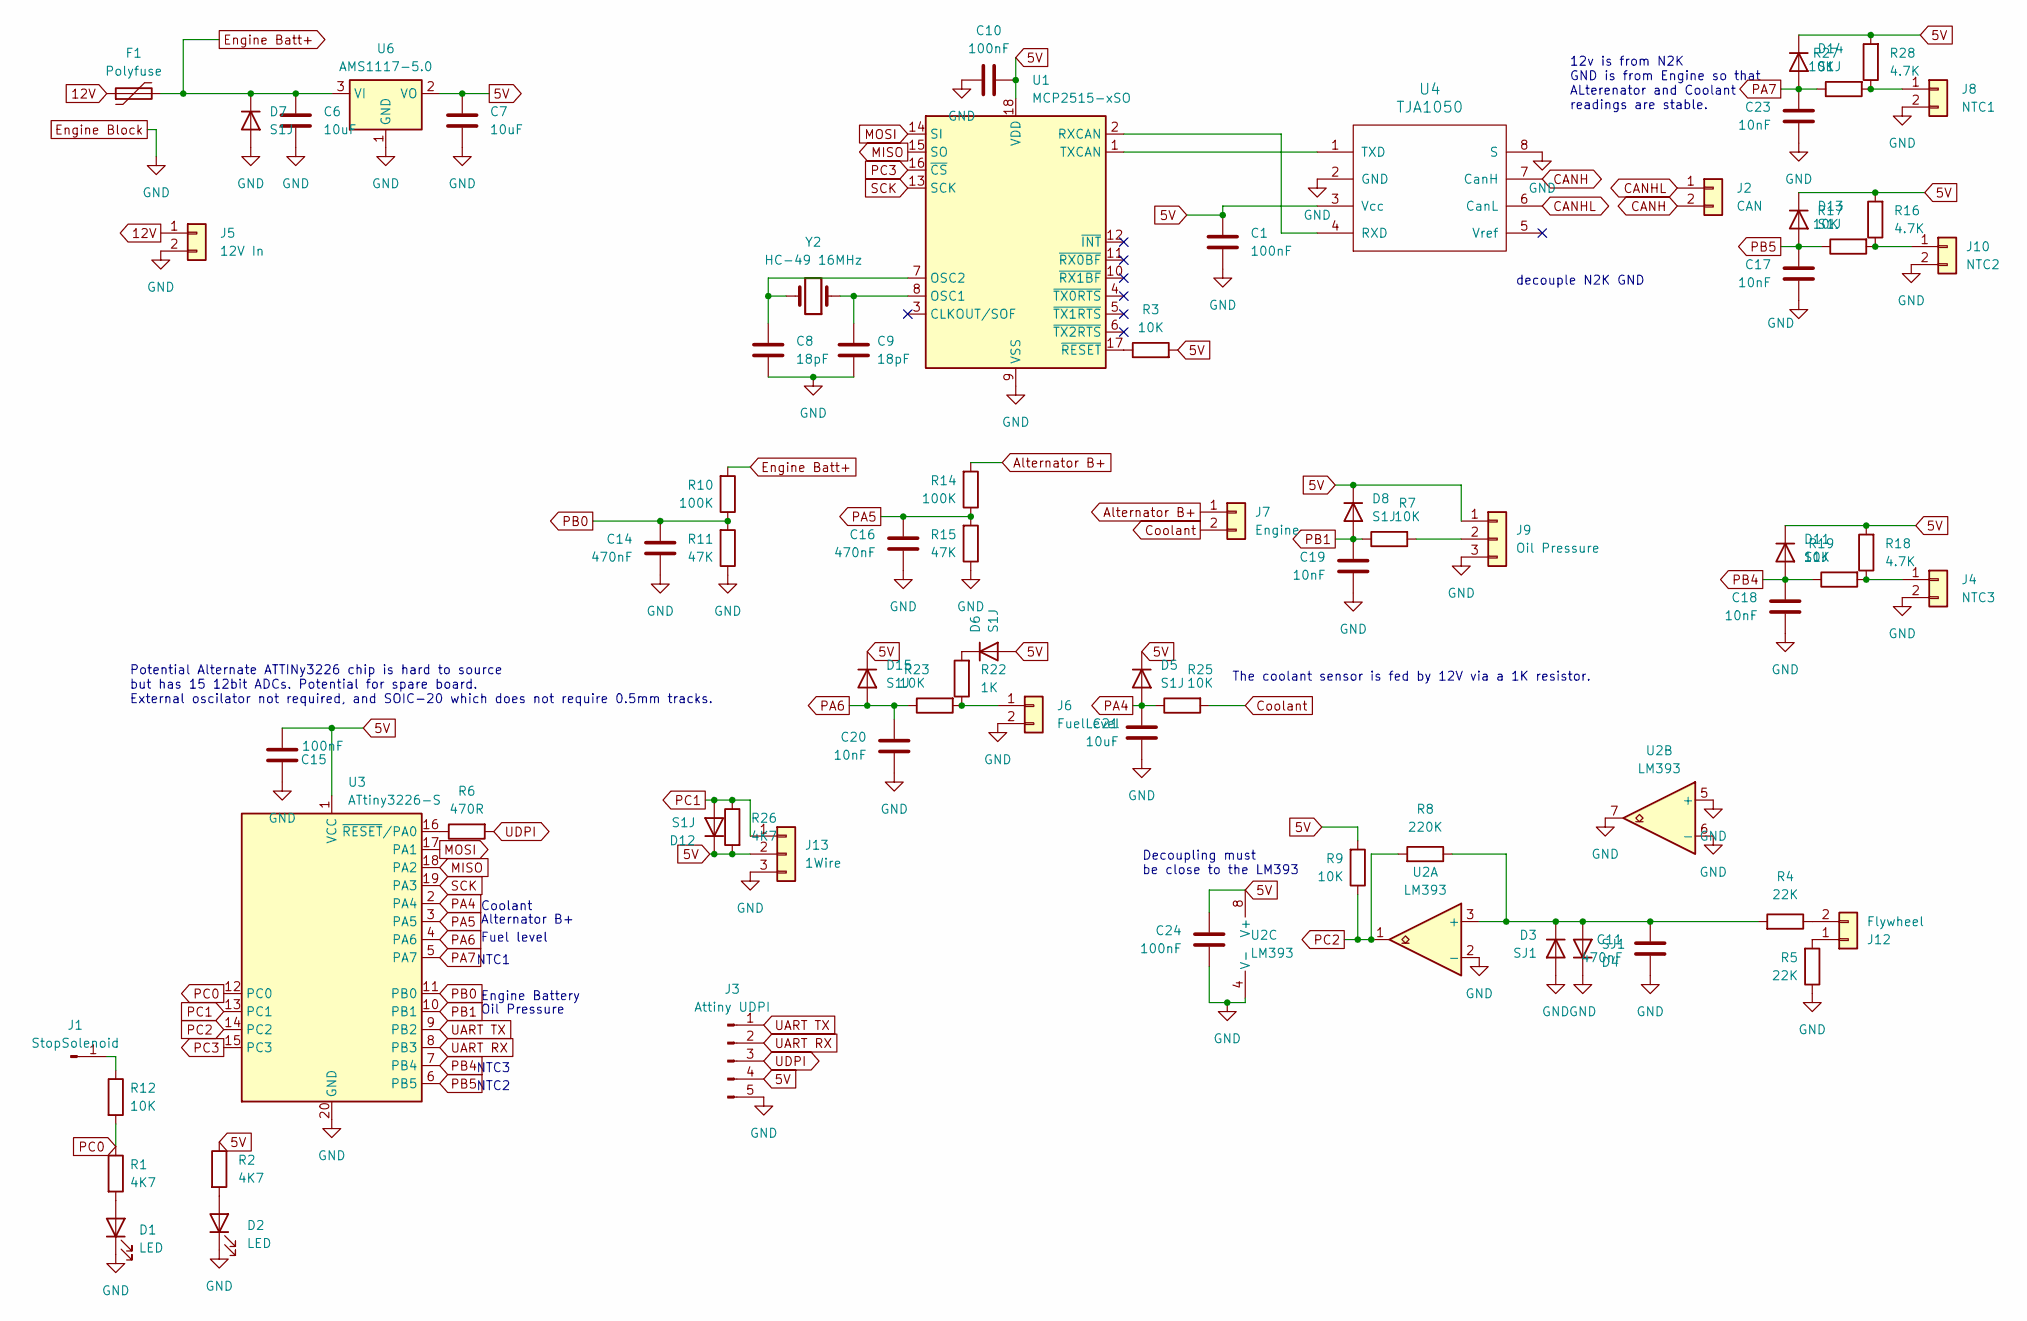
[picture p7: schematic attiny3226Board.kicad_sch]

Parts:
C1, C10, C15, C24: 100nF; C_0805_2012Metric_Pad1.18x1.45mm_HandSolder
C6, C7: 10uF; C_1206_3216Metric_Pad1.33x1.80mm_HandSolder
C8, C9: 18pF; C_0805_2012Metric_Pad1.18x1.45mm_HandSolder
C11, C14, C16: 470nF; C_0805_2012Metric_Pad1.18x1.45mm_HandSolder
C17, C18, C19, C20, C23: 10nF; C_0805_2012Metric_Pad1.18x1.45mm_HandSolder
C21: 10uF; C_0805_2012Metric_Pad1.18x1.45mm_HandSolder
D1, D2: LED; LED_0805_2012Metric_Pad1.15x1.40mm_HandSolder
D3, D4: SJ1; D_SOD-123
D5, D6, D7, D8, D11, D12, D13, D14, D15: S1J; D_0805_2012Metric_Pad1.15x1.40mm_HandSolder
F1: Polyfuse; Fuse_1812_4532Metric_Pad1.30x3.40mm_HandSolder
J1: StopSolenoid; PinSocket_1x01_P2.54mm_Vertical
J2: CAN; TerminalBlock_Phoenix_MKDS-1,5-2-5.08_1x02_P5.08mm_Horizont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
J3: Attiny UDPI; PinHeader_1x05_P2.54mm_Vertical
J4: NTC3; TerminalBlock_Phoenix_MKDS-1,5-2-5.08_1x02_P5.08mm_Horizont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
J5: 12V In; TerminalBlock_Phoenix_MKDS-1,5-2-5.08_1x02_P5.08mm_Horizont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
J6: FuelLevel; TerminalBlock_Phoenix_MKDS-1,5-2-5.08_1x02_P5.08mm_Horizont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
J7: Engine; TerminalBlock_Phoenix_MKDS-1,5-2-5.08_1x02_P5.08mm_Horizont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
J8: NTC1; TerminalBlock_Phoenix_MKDS-1,5-2-5.08_1x02_P5.08mm_Horizont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
J9: Oil Pressure; TerminalBlock_Phoenix_MKDS-1,5-3-5.08_1x03_P5.08mm_Horizont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
J10: NTC2; TerminalBlock_Phoenix_MKDS-1,5-2-5.08_1x02_P5.08mm_Horizont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
J12: Flywheel; TerminalBlock_Phoenix_MKDS-1,5-2-5.08_1x02_P5.08mm_Horizont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
J13: 1Wire; TerminalBlock_Phoenix_MKDS-1,5-3-5.08_1x03_P5.08mm_Horizont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
R1, R2, R26: 4K7; R_0805_2012Metric_Pad1.20x1.40mm_HandSolder
R3, R7, R9, R12, R17, R19, R23, R25, R27: 10K; R_0805_2012Metric_Pad1.20x1.40mm_HandSolder
R4, R5: 22K; R_0805_2012Metric_Pad1.20x1.40mm_HandSolder
R6: 470R; R_0805_2012Metric_Pad1.20x1.40mm_HandSolder
R8: 220K; R_0805_2012Metric_Pad1.20x1.40mm_HandSolder
R10, R14: 100K; R_0805_2012Metric_Pad1.20x1.40mm_HandSolder
R11, R15: 47K; R_0805_2012Metric_Pad1.20x1.40mm_HandSolder
R16, R18, R28: 4.7K; R_0805_2012Metric_Pad1.20x1.40mm_HandSolder
R22: 1K; R_0805_2012Metric_Pad1.20x1.40mm_HandSolder
U1: MCP2515-xSO; SOIC-18W_7.5x11.6mm_P1.27mm
U2: LM393; SOIC-8_3.9x4.9mm_P1.27mm
U3: ATtiny3226-S; SOIC-20W_7.5x12.8mm_P1.27mm
U4: TJA1050; SOIC-8_3.9x4.9mm_P1.27mm
U6: AMS1117-5.0; SOT-223-3_TabPin2
Y2: HC-49 16MHz; Crystal_SMD_HC49-SD

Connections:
5V: C1.1, C7.1, C10.2, C15.2, C24.2, D5.1 (K), D6.2 (A), D8.1 (K), D11.1 (K), D12.1 (K), D13.1 (K), D14.1 (K), D15.1 (K), J3.4, J9.1, J13.2, R2.1, R3.2, R9.2, R16.2, R18.2, R26.2, R28.2, U1.18 (VDD), U2.8 (V+), U3.1 (VCC), U4.3 (Vcc), U6.2 (VO)
12V: F1.1, J5.1
Alternator B+: J7.1, R14.2
CANH: J2.2, U4.7 (CanH)
CANHL: J2.1, U4.6 (CanL)
Coolant: J7.2, R25.2
Engine Batt+: C6.1, D7.1 (K), F1.2, R10.2, U6.3 (VI)
Engine Block: C1.2, C6.2, C7.2, C8.1, C9.1, C10.1, C11.1, C14.1, C15.1, C16.1, C17.1, C18.1, C19.1, C20.1, C21.1, C23.1, C24.1, D1.1 (K), D2.1 (K), D3.2 (A), D4.1 (K), D7.2 (A), J3.5, J4.2, J5.2, J6.2, J8.2, J9.3, J10.2, J13.3, R5.1, R11.1, R15.1, U1.9 (VSS), U2.2 (-), U2.4 (V-), U2.5 (+), U2.6 (-), U2.7, U3.20 (GND), U4.2 (GND), U4.8 (S), U6.1 (GND)
MISO: U1.15 (SO), U3.18 (PA2)
MOSI: U1.14 (SI), U3.17 (PA1)
unnamed: D1.2 (A), R1.2
unnamed: D2.2 (A), R2.2
unnamed: C11.2, D3.1 (K), D4.2 (A), R4.2, R8.1, U2.3 (+)
unnamed: D6.1 (K), R22.2
unnamed: J1.1, R12.1
unnamed: J4.1, R18.1, R19.2
unnamed: J6.1, R22.1, R23.2
unnamed: J8.1, R27.2, R28.1
unnamed: J9.2, R7.2
unnamed: J10.1, R16.1, R17.2
unnamed: J12.1, R5.2
unnamed: J12.2, R4.1
unnamed: C9.2, U1.8 (OSC1), Y2.1
unnamed: C8.2, U1.7 (OSC2), Y2.2
unnamed: U1.2 (RXCAN), U4.4 (RXD)
unnamed: U1.1 (TXCAN), U4.1 (TXD)
unnamed: R3.1, U1.17 (~RESET)
unnamed: R6.1, U3.16 (~RESET/PA0)
PA4: C21.2, D5.2 (A), R25.1, U3.2 (PA4)
PA5: C16.2, R14.1, R15.2, U3.3 (PA5)
PA6: C20.2, D15.2 (A), R23.1, U3.4 (PA6)
PA7: C23.2, D14.2 (A), R27.1, U3.5 (PA7)
PB0: C14.2, R10.1, R11.2, U3.11 (PB0)
PB1: C19.2, D8.2 (A), R7.1, U3.10 (PB1)
PB4: C18.2, D11.2 (A), R19.1, U3.7 (PB4)
PB5: C17.2, D13.2 (A), R17.1, U3.6 (PB5)
PC0: R1.1, R12.2, U3.12 (PC0)
PC1: D12.2 (A), J13.1, R26.1, U3.13 (PC1)
PC2: R8.2, R9.1, U2.1, U3.14 (PC2)
PC3: U1.16 (~CS), U3.15 (PC3)
SCK: U1.13 (SCK), U3.19 (PA3)
UART RX: J3.2, U3.8 (PB3)
UART TX: J3.1, U3.9 (PB2)
UDPI: J3.3, R6.2

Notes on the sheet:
Alternator B+
Oil Pressure
NTC2
NTC1
12v is from N2K GND is from Engine so that ALterenator and Coolant readings are stable.
Coolant
The coolant sensor is fed by 12V via a 1K resistor.
Fuel level
Engine Battery
decouple N2K GND
Potential Alternate ATTINy3226 chip is hard to source but has 15 12bit ADCs. Potential for spare board. External oscilator not required, and SOIC-20 which does not require 0.5mm tracks.
NTC3
Decoupling must be close to the LM393

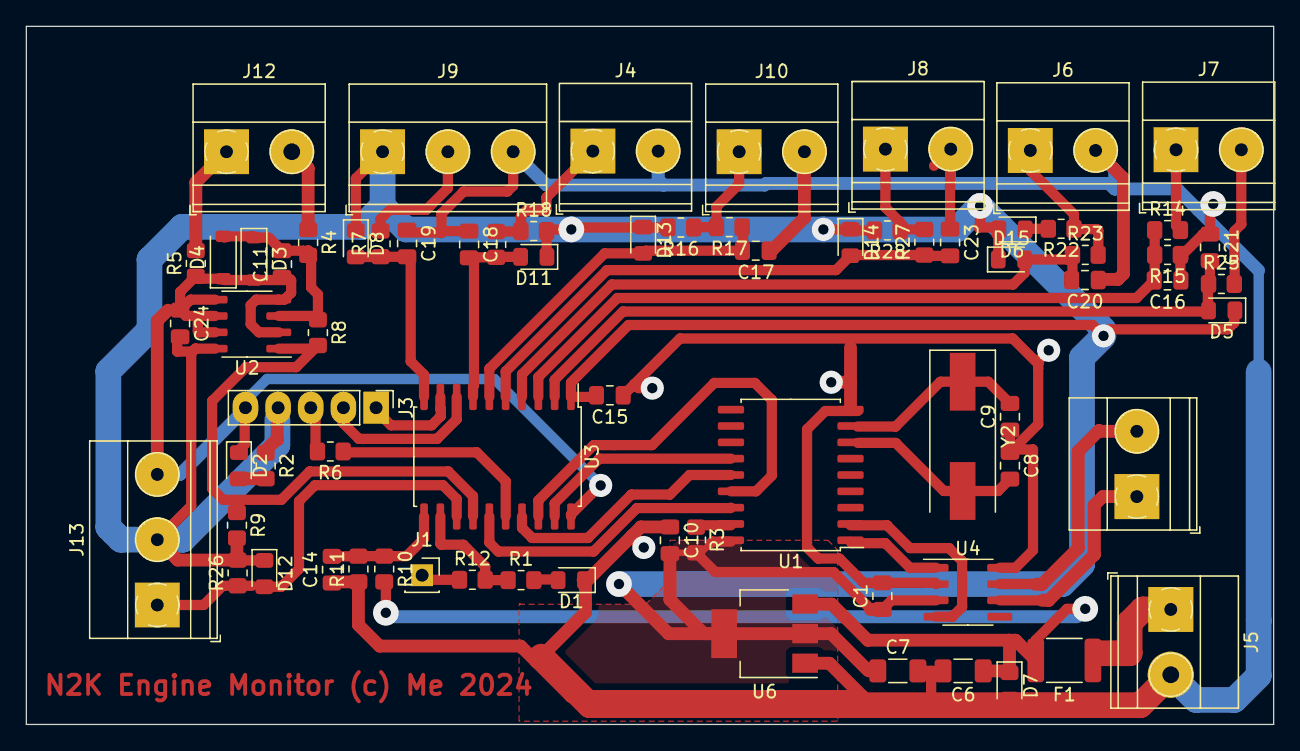
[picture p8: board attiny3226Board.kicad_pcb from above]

Board: 2 copper layers, 97.0 x 54.3 mm, 73 parts (0 on the bottom side), 44 nets.

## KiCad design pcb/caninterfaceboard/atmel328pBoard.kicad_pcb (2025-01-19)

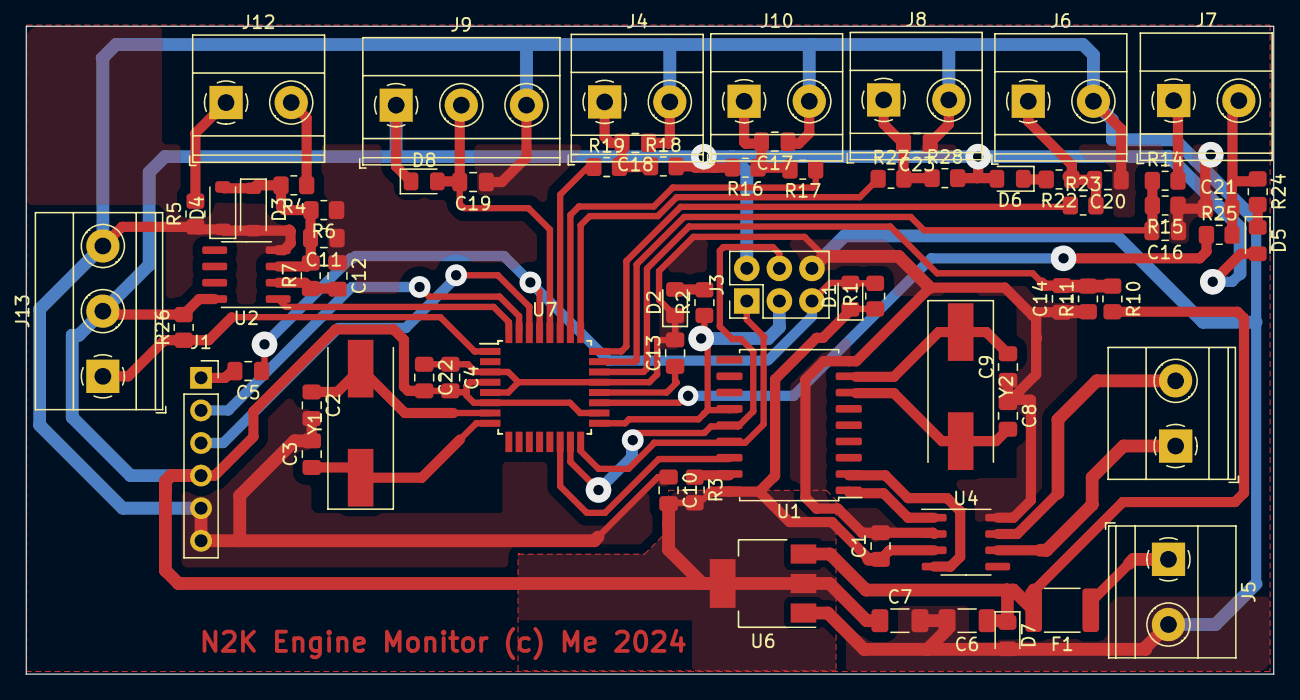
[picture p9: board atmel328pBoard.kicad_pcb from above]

Board: 2 copper layers, 97.2 x 50.5 mm, 72 parts (0 on the bottom side), 45 nets.

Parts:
C1, C4, C5, C10, C13, C22: 100nF; C_0805_2012Metric_Pad1.18x1.45mm_HandSolder
C2, C3, C8, C9: 18pF; C_0805_2012Metric_Pad1.18x1.45mm_HandSolder
C6, C7: 10uF; C_1206_3216Metric_Pad1.33x1.80mm_HandSolder
C11, C12: 1uF; C_0805_2012Metric_Pad1.18x1.45mm_HandSolder
C14, C16: 1nF; C_0805_2012Metric_Pad1.18x1.45mm_HandSolder
C17, C18, C19, C20, C21, C23: 10nF; C_0805_2012Metric_Pad1.18x1.45mm_HandSolder
D1, D5, D6, D7, D8: S1J; D_0805_2012Metric_Pad1.15x1.40mm_HandSolder
D2: LED; LED_0805_2012Metric_Pad1.15x1.40mm_HandSolder
D3, D4: 1N5819; D_SOD-123
F1: Polyfuse; Fuse_1812_4532Metric_Pad1.30x3.40mm_HandSolder
J1: UART; PinSocket_1x06_P2.54mm_Vertical
J2: CAN; TerminalBlock_Phoenix_MKDS-1,5-2-5.08_1x02_P5.08mm_Horizont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
J3: AVR ISP; PinHeader_2x03_P2.54mm_Vertical
J4: NTC3; TerminalBlock_Phoenix_MKDS-1,5-2-5.08_1x02_P5.08mm_Horizont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
J5: 12V In; TerminalBlock_Phoenix_MKDS-1,5-2-5.08_1x02_P5.08mm_Horizont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
J6: FuelLevel; TerminalBlock_Phoenix_MKDS-1,5-2-5.08_1x02_P5.08mm_Horizont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
J7: Engine; TerminalBlock_Phoenix_MKDS-1,5-2-5.08_1x02_P5.08mm_Horizont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
J8: NTC1; TerminalBlock_Phoenix_MKDS-1,5-2-5.08_1x02_P5.08mm_Horizont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
J9: Oil Pressure; TerminalBlock_Phoenix_MKDS-1,5-3-5.08_1x03_P5.08mm_Horizont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
J10: NTC2; TerminalBlock_Phoenix_MKDS-1,5-2-5.08_1x02_P5.08mm_Horizont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
J12: Flywheel; TerminalBlock_Phoenix_MKDS-1,5-2-5.08_1x02_P5.08mm_Horizont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
J13: 1Wire; TerminalBlock_Phoenix_MKDS-1,5-3-5.08_1x03_P5.08mm_Horizont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
R1, R3: 10K; R_0805_2012Metric_Pad1.20x1.40mm_HandSolder
R2: 330R; R_0805_2012Metric_Pad1.20x1.40mm_HandSolder
R4, R5: 22K; R_0805_2012Metric_Pad1.20x1.40mm_HandSolder
R6, R22, R24: 1K; R_0805_2012Metric_Pad1.20x1.40mm_HandSolder
R7, R17, R19, R23, R25, R27: 100K; R_0805_2012Metric_Pad1.20x1.40mm_HandSolder
R10, R14: 1M; R_0805_2012Metric_Pad1.20x1.40mm_HandSolder
R11, R15: 470K; R_0805_2012Metric_Pad1.20x1.40mm_HandSolder
R16, R18, R28: 4.7K; R_0805_2012Metric_Pad1.20x1.40mm_HandSolder
R26: 4K7; R_0805_2012Metric_Pad1.20x1.40mm_HandSolder
U1: MCP2515-xSO; SOIC-18W_7.5x11.6mm_P1.27mm
U2: LM393; SOIC-8_3.9x4.9mm_P1.27mm
U4: TJA1050; SOIC-8_3.9x4.9mm_P1.27mm
U6: AMS1117-5.0; SOT-223-3_TabPin2
U7: ATmega328P-A; TQFP-32_7x7mm_P0.8mm
Y1, Y2: HC-49 16MHz; Crystal_SMD_HC49-SD

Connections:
5V: C1.1, C4.2, C7.1, C10.2, C22.2, D1.1 (K), D5.2 (A), D6.2 (A), D8.1 (K), J1.4, J3.2, J9.1, J13.2, R1.1, R3.2, R16.2, R18.2, R26.2, R28.2, U1.18 (VDD), U2.8 (V+), U4.3 (Vcc), U6.2 (VO), U7.4 (VCC), U7.6 (VCC), U7.18 (AVCC)
12V: F1.1, J5.1
A0: C16.2, R14.1, R15.2, U7.23 (PC0)
A1: R23.1, U7.24 (PC1)
A2: R27.1, U7.25 (PC2)
A3: R17.1, U7.26 (PC3)
A4: R19.1, U7.27 (PC4)
A5: C19.2, D8.2 (A), J9.2, U7.28 (PC5)
A6: R25.1, U7.19 (ADC6)
A7: C14.2, R10.1, R11.2, U7.22 (ADC7)
Alternator B+: J7.1, R14.2
CANH: J2.2, U4.7 (CanH)
CANHL: J2.1, U4.6 (CanL)
Coolant: C21.2, J7.2, R24.1, R25.2
D2: U2.1, U7.32 (PD2)
D3: J13.1, R26.1, U7.1 (PD3)
D10: U1.16 (~CS), U7.14 (PB2)
Engine Batt+: C6.1, D7.1 (K), F1.2, R10.2, U6.3 (VI)
Engine Block: C1.2, C2.2, C3.2, C4.1, C6.2, C7.2, C8.1, C9.1, C10.1, C11.1, C12.1, C13.2, C14.1, C16.1, C17.1, C18.1, C19.1, C20.1, C21.1, C22.1, C23.1, D2.1 (K), D3.2 (A), D4.1 (K), D7.2 (A), J1.5, J1.6, J3.6, J4.2, J5.2, J6.2, J8.2, J9.3, J10.2, J13.3, R5.1, R6.1, R11.1, R15.1, U1.9 (VSS), U2.4 (V-), U4.2 (GND), U4.8 (S), U6.1 (GND), U7.3 (GND), U7.5 (GND), U7.21 (GND)
ISP RST: C5.1, D1.2 (A), J3.5, R1.2, U7.29 (~RESET/PC6)
MISO: J3.1, U1.15 (SO), U7.16 (PB4)
MOSI: J3.4, U1.14 (SI), U7.15 (PB3)
unnamed: D2.2 (A), R2.2
unnamed: C11.2, D3.1 (K), D4.2 (A), R4.2, R6.2, R7.2, U2.3 (+)
unnamed: D5.1 (K), R24.2
unnamed: D6.1 (K), R22.2
unnamed: C18.2, J4.1, R18.1, R19.2
unnamed: C20.2, J6.1, R22.1, R23.2
unnamed: C23.2, J8.1, R27.2, R28.1
unnamed: C17.2, J10.1, R16.1, R17.2
unnamed: J12.1, R5.2
unnamed: J12.2, R4.1
unnamed: C9.2, U1.8 (OSC1), Y2.1
unnamed: C8.2, U1.7 (OSC2), Y2.2
unnamed: U1.2 (RXCAN), U4.4 (RXD)
unnamed: U1.1 (TXCAN), U4.1 (TXD)
unnamed: R3.1, U1.17 (~RESET)
unnamed: C12.2, R7.1, U2.2 (-)
unnamed: C13.1, U7.20 (AREF)
SCK: J3.3, R2.1, U1.13 (SCK), U7.17 (PB5)
UART DTR: C5.2, J1.1
UART RX: J1.2, U7.31 (PD1)
UART TX: J1.3, U7.30 (PD0)
XTAL1: C2.1, U7.7 (XTAL1/PB6), Y1.2
XTAL2: C3.1, U7.8 (XTAL2/PB7), Y1.1

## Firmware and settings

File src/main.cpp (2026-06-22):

#include "version.h"
#include <Arduino.h>
#include "enginesensors.h"
#include "SmallNMEA2000.h"
#include <MemoryFree.h>
#ifndef INSPECT_FLASH_USAGE
#include "oneWireSensors.h"
#endif

#define RAPID_ENGINE_UPDATE_PERIOD 500
#define ENGINE_UPDATE_PERIOD 1000
#define VOLTAGE_UPDATE_PERIOD 999
#define FUEL_UPDATE_PERIOD 4900
#define TEMPERATURE_UPDATE_PERIOD 4850

#define ENGINE_INSTANCE 0
#define ENGINE_BATTERY_INSTANCE 0
// treating the alternator as a battery its possible to monitor temperature.
#define ALTERNATOR_BATTERY_INSTANCE 2
// Now using a dedicated shunt for service battery #define SERVICE_BATTERY_INSTANCE 2
#define FUEL_LEVEL_INSTANCE 0
#define FUEL_TYPE 0   // diesel


// ADC assignments

#ifdef __AVR_TINY_2__

#define ADC_ALTERNATOR_VOLTAGE PIN_PA5
#define ADC_FUEL_SENSOR PIN_PA6
#define ADC_EXHAUST_NTC1 PIN_PA7 // NTC1
#define ADC_ALTERNATOR_NTC2 PIN_PB5 // NTC2
#define ADC_ENGINEROOM_NTC3 PIN_PB4
#define ADC_OIL_SENSOR PIN_PB1
#define ADC_COOLANT_TEMPERATURE PIN_PA4
#define ADC_ENGINEBATTERY PIN_PB0


#define PIN_FLYWHEEL PIN_PC2
#define PIN_ONE_WIRE ONE_WIRE_PIN 

#define SNMEA_SPI_M0SI PIN_PA1 // Default pin
#define SNMEA_SPI_MISO PIN_PA2 // Default Pin
#define SNMEA_SPI_SCK  PIN_PA3 // Default pin
#define SNMEA_SPI_CS_PIN  PIN_PC3 // not default, set in constructor
#define LED_PIN PIN_PC0

#else

#define ADC_ALTERNATOR_VOLTAGE 0
#define ADC_FUEL_SENSOR 1
#define ADC_EXHAUST_NTC1 2 // NTC1
#define ADC_ALTERNATOR_NTC2 3 // NTC2
#define ADC_ENGINEROOM_NTC3 4
#define ADC_OIL_SENSOR 5
#define ADC_COOLANT_TEMPERATURE 6
#define ADC_ENGINEBATTERY 7
// Digital pin assignments
// Flywheel pulse pin
#define PIN_FLYWHEEL 2
#define PIN_ONE_WIRE 3 // not used at present


// defaults
#define SNMEA_SPI_M0SI 11 
#define SNMEA_SPI_MISO 12 
#define SNMEA_SPI_SCK  13 
#define SNMEA_SPI_CS_PIN 10
#endif






#define DEVICE_ADDRESS 24

#define ENGINE_PROPRIETARY_PGN  65305L
#define ENGINE_PROPRIETARY_FP_PGN  130817L
#define ENGINE_PROPRIETARY_CODE 0x9ffe // 2046 & 0x7FE | 0x3<<11 | 0x04<<13
#define FN_DUMP_EVENTS 11
#define FN_DUMP_EVENTS_RESP 12
#define FN_CLEAR_EVENTS 13
#define FN_CLEAR_EVENTS_RESP 14


bool sensorDebug = false;
bool monitorEnabled = false;

EngineSensors sensors(PIN_FLYWHEEL, 
    ADC_ALTERNATOR_VOLTAGE,
    ADC_ENGINEBATTERY,
    ADC_EXHAUST_NTC1,
    ADC_ALTERNATOR_NTC2,
    ADC_ENGINEROOM_NTC3);


const SNMEA2000ProductInfo productInfomation PROGMEM={
                                       1300,                        // N2kVersion
                                       44,                         // Manufacturer's product code
                                       "EMS",    // Manufacturer's Model ID
                                       "1.2.3.4 (2023-05-16)",     // Manufacturer's Software version code
                                       "5.6.7.8 (2017-06-11)",      // Manufacturer's Model version
                                       "0000002",                  // Manufacturer's Model serial code
                                       0,                           // SertificationLevel
                                       1                            // LoadEquivalency
};
const SNMEA2000ConfigInfo configInfo PROGMEM={
      "Engine Monitor",
      "Luna Technical Area",
      "https://github.com/ieb/EngineManagement"
};


const unsigned long txPGN[] = { 
    127488L, // Rapid engine ideally 0.1s
    127489L, // Dynamic engine 0.5s
    127505L, // Tank Level 2.5s
    130316L, // Extended Temperature 2.5s
    127508L,
  SNMEA200_DEFAULT_TX_PGN
};

const unsigned long rxPGN[] = { 
  ENGINE_PROPRIETARY_PGN,
  ENGINE_PROPRIETARY_FP_PGN,
  SNMEA200_DEFAULT_RX_PGN
};

SNMEA2000DeviceInfo devInfo = SNMEA2000DeviceInfo(
  223,   // device serial number
  140,  // Engine
  50 // Propulsion
);



EngineMonitor engineMonitor = EngineMonitor(DEVICE_ADDRESS,
  &devInfo,
  &productInfomation, 
  &configInfo, 
  &txPGN[0],
  SNMEA200_DEFAULT_TX_PGN_LEN+5,
  &rxPGN[0],
  SNMEA200_DEFAULT_RX_PGN_LEN+2,
  SNMEA_SPI_CS_PIN);

#ifndef INSPECT_FLASH_USAGE
OneWire oneWire;
OneWireSensors oneWireSensor(oneWire);
#endif

#ifdef LED_PIN
void toggleLed() {
  digitalWrite(LED_PIN, !digitalRead(LED_PIN));
}
void asyncBlink() {
  static unsigned long lastToggle=0;
  unsigned long now = millis();
  if ( now-lastToggle > 5000 ) {
    lastToggle = now;
    toggleLed();
  }
}

void setupLed() {
  pinMode(LED_PIN, OUTPUT);
  digitalWrite(LED_PIN, LOW);
}
void blinkLed(int n) {
  for (int i = 0; i < n; i++) {
    digitalWrite(LED_PIN, HIGH);
    delay(100);
    digitalWrite(LED_PIN, LOW);
    delay(100);    
  }
}


#else
void setupLed(){};
void asyncBlink(){};
void toggleLed(){};
void blinkLed(int n){};
#endif



/**
 * Send engine rapid updates while the engine is running.
 */ 
void sendRapidEngineData() {
  static unsigned long lastRapidEngineUpdate=0;
  if ( sensors.isEngineRunning() ) {
    unsigned long now = millis();
    if ( now-lastRapidEngineUpdate > RAPID_ENGINE_UPDATE_PERIOD ) {
      lastRapidEngineUpdate = now;
      toggleLed();
      engineMonitor.sendRapidEngineDataMessage(ENGINE_INSTANCE, sensors.getEngineRPM());
    }
  }
}


/**
 * Send engine status while the engine is running.
 */ 
void sendEngineData() {
  static unsigned long lastEngineUpdate=0;
  if ( sensors.isEngineRunning() ) {
    unsigned long now = millis();
    if ( now-lastEngineUpdate > ENGINE_UPDATE_PERIOD ) {
      lastEngineUpdate = now;
      toggleLed();
      double engineSeconds = sensors.getEngineSeconds();
      double coolantTemperature = sensors.getCoolantTemperatureK(ADC_COOLANT_TEMPERATURE, ADC_ENGINEBATTERY);
      double alternatorVoltage = sensors.getVoltage(ADC_ALTERNATOR_VOLTAGE);
      double oilPressure = sensors.getOilPressure(ADC_OIL_SENSOR);
      double alternatorTemperature = sensors.getTemperatureK(ADC_ALTERNATOR_NTC2);
      double exhaustTemperature = sensors.getTemperatureK(ADC_EXHAUST_NTC1);



      uint16_t status1 = sensors.getEngineStatus1();
      uint16_t status2 = sensors.getEngineStatus2();
      if (status1 != 0) {
        sensors.dumpEngineStatus1();
      }
      if (status2 != 0) {
        sensors.dumpEngineStatus2();
      }
      engineMonitor.sendEngineDynamicParamMessage(ENGINE_INSTANCE,
          engineSeconds,
          coolantTemperature,
          alternatorVoltage,
          status1, // status1
          status2, // status2
          oilPressure, // engineOilPressure
          alternatorTemperature // alterator temperature as engineOil temperature, more important with LiFeP04
          );
    }
  }
}

/**
 * Send voltages all the time.
 */ 
void sendVoltages() {
  static unsigned long lastVoltageUpdate=0;
  static byte sid = 0;
  unsigned long now = millis();
  if ( now-lastVoltageUpdate > VOLTAGE_UPDATE_PERIOD ) {
    lastVoltageUpdate = now;
      toggleLed();
    // because the engine monitor is not on all the time, the sid and instance ids of these messages has been shifted
    // to make space for sensors that are on all the time, and would be used by default
    // engineMonitor.sendDCBatterStatusMessage(SERVICE_BATTERY_INSTANCE, sid, sensors.getServiceBatteryVoltage());
    engineMonitor.sendDCBatterStatusMessage(ENGINE_BATTERY_INSTANCE, sid, sensors.getVoltage(ADC_ENGINEBATTERY));
    engineMonitor.sendDCBatterStatusMessage(ALTERNATOR_BATTERY_INSTANCE, sid, 
        sensors.getVoltage(ADC_ALTERNATOR_VOLTAGE),
        sensors.getTemperatureK(ADC_ALTERNATOR_NTC2)
        );
    sid++;
  }
}

/**
 * send Fuel all the time.
 */ 
void sendFuel() {
  static unsigned long lastFuelUpdate=0;
  unsigned long now = millis();
  if ( now-lastFuelUpdate > FUEL_UPDATE_PERIOD ) {
    lastFuelUpdate = now;
      toggleLed();
    engineMonitor.sendFluidLevelMessage(FUEL_TYPE, FUEL_LEVEL_INSTANCE, sensors.getFuelLevel(ADC_FUEL_SENSOR), sensors.getFuelCapacity());
  }
}

/**
 * send temperatures all the time.
 */ 
void sendTemperatures() {
  static unsigned long lastTempUpdate=0;
  static byte sid = 0;
  unsigned long now = millis();
  if ( now-lastTempUpdate > TEMPERATURE_UPDATE_PERIOD ) {
    lastTempUpdate = now;    
      toggleLed();
    // this may need adjusting depending on what the instruments can display
    double exhaustTemperature = sensors.getTemperatureK(ADC_EXHAUST_NTC1);
    engineMonitor.sendTemperatureMessage(sid, 0, 14, exhaustTemperature);
    // abusing transmission information so exhaust temp can be shown on an i70 display
    engineMonitor.sendTransmissionDynamicParamMessage(ENGINE_INSTANCE,
        0x03, // invalid transmssionGear,
        -1E9, //transmssionOilPressure,
        exhaustTemperature,
        0x00); // transmissionStatus
    engineMonitor.sendTemperatureMessage(sid, 0, 3, sensors.getTemperatureK(ADC_ENGINEROOM_NTC3));
    // custom temperatures
    // temperature source can be 0-255, 0-15 are defined.
    engineMonitor.sendTemperatureMessage(sid, 0, 30, sensors.getTemperatureK(ADC_ALTERNATOR_NTC2));

#ifndef INSPECT_FLASH_USAGE
    uint8_t maxActiveDevices = oneWireSensor.getMaxActiveDevice();
    for (int i = 0; i < maxActiveDevices; i++) {
      engineMonitor.sendTemperatureMessage(sid, 0, 31+i, oneWireSensor.getTemperatureK(i));
    }
#endif
    sid++;
  }
}


void printN2K(double v, double fact, double offset, const char * term="\n") {
  if ( v == SNMEA2000::n2kDoubleNA) {
    Serial.print(F("--"));
  } else {
    Serial.print((v*fact)-offset);
  }
  Serial.print(term);
}


// uses 1.1KB
void showStatus() {
  Serial.print(F("CPU Vdd   : "));Serial.println(sensors.getStoredVddVoltage());
  Serial.print(F("Free mem  : "));Serial.println(freeMemory());
  Serial.print(F("Exhaust T : "));printN2K(sensors.getTemperatureK(ADC_EXHAUST_NTC1, sensorDebug), 1.0,273.15);
  Serial.print(F("Alt T     : "));printN2K(sensors.getTemperatureK(ADC_ALTERNATOR_NTC2, sensorDebug),1.0, 273.15);
  Serial.print(F("Room T    : "));printN2K(sensors.getTemperatureK(ADC_ENGINEROOM_NTC3, sensorDebug),1.0,273.15);
  Serial.print(F("Fuel      : "));printN2K(sensors.getFuelLevel(ADC_FUEL_SENSOR, sensorDebug),1.0,0);
  Serial.print(F("Engine V  : "));printN2K(sensors.getVoltage(ADC_ENGINEBATTERY, sensorDebug),1.0,0);
  Serial.print(F("Alt V     : "));printN2K(sensors.getVoltage(ADC_ALTERNATOR_VOLTAGE, sensorDebug),1.0,0);
  Serial.print(F("Engine h  : "));Serial.println(sensors.getEngineSeconds()/3600.0);
  Serial.print(F("Coolant T : "));printN2K(sensors.getCoolantTemperatureK(ADC_COOLANT_TEMPERATURE, ADC_ENGINEBATTERY, sensorDebug),1.0,273.15);
  Serial.print(F("Oil Psi   : "));printN2K(sensors.getOilPressure(ADC_OIL_SENSOR, sensorDebug),1.0/6894.76,0.0);
  sensors.read(sensorDebug);
  Serial.print(F("Engine On : "));Serial.println(sensors.isEngineRunning()?"Y":"N");
  Serial.print(F("Engine RPM: "));printN2K(sensors.getEngineRPM(),1.0,0);
#ifndef INSPECT_FLASH_USAGE
  uint8_t maxActiveDevices = oneWireSensor.getMaxActiveDevice();
  Serial.print(F("Onewire N : "));Serial.println(maxActiveDevices);
  for (int i = 0; i < maxActiveDevices; i++) {
    Serial.print(F("    "));
    Serial.print(i);
    Serial.print(F(" : "));
    printN2K(oneWireSensor.getTemperatureK(i),1.0,273.15);
  }
#endif
  engineMonitor.dumpStatus();


  Serial.print(F("ADC_EXH  : "));sensors.dumpADC(ADC_EXHAUST_NTC1);
  Serial.print(F("ADC_ALT  : "));sensors.dumpADC(ADC_ALTERNATOR_NTC2);
  Serial.print(F("ADC_ROOM : "));sensors.dumpADC(ADC_ENGINEROOM_NTC3);
  Serial.print(F("ADC_ALT_V: "));sensors.dumpADC(ADC_ALTERNATOR_VOLTAGE);
  Serial.print(F("ADC_FUEL : "));sensors.dumpADC(ADC_FUEL_SENSOR);
  Serial.print(F("ADC_OIL  : "));sensors.dumpADC(ADC_OIL_SENSOR);
  Serial.print(F("ADC_COOL : "));sensors.dumpADC(ADC_COOLANT_TEMPERATURE);
  Serial.print(F("ADC_BAT  : "));sensors.dumpADC(ADC_ENGINEBATTERY);

  sensors.dumpEngineStatus1();
  sensors.dumpEngineStatus2();

  // dump the stored events
  uint32_t lastEvent = 0;
  Serial.print(F("Stored Events:"));
  Serial.println(sensors.localStorage.countEvents());
  for (int i = 0; i < 30; ++i) {
    uint8_t eventId = sensors.localStorage.nextEvent(lastEvent);
    if ( eventId == EVENTS_NO_EVENT) {
      break;
    }
    Serial.print(F("evt:"));
    Serial.print(eventId);
    Serial.print(F(" h:"));
    Serial.println(0.004166666667*lastEvent);
  }


}

void monitor() {
  static unsigned long lastMonitorOutput = 0;
  if ( monitorEnabled) {
    unsigned long now = millis();
    if ( now-lastMonitorOutput > 1000 ) {
      lastMonitorOutput = now;
      Serial.print("rpm=");
      printN2K(sensors.getEngineRPM(),1.0,0,",");
      Serial.print(" coolant=");
      printN2K(sensors.getCoolantTemperatureK(ADC_COOLANT_TEMPERATURE, ADC_ENGINEBATTERY, false),1.0, 273.15, ",");
      Serial.print(" oil=");
      printN2K(sensors.getOilPressure(ADC_OIL_SENSOR, false),1.0/6894.76,0.0, ",");
      Serial.print(" fuel=");
      printN2K(sensors.getFuelLevel(ADC_FUEL_SENSOR, false),1.0, 0.0, ",");
      Serial.print(" batV=");
      printN2K(sensors.getVoltage(ADC_ENGINEBATTERY, false), 1.0, 0.0, ",");
      Serial.print(" altV=");
      printN2K(sensors.getVoltage(ADC_ALTERNATOR_VOLTAGE, false),1.0, 0.0, ",");
      Serial.print(" exT=");
      printN2K(sensors.getTemperatureK(ADC_EXHAUST_NTC1, false), 1.0, 273.15, ",");
      Serial.print(" altT=");
      printN2K(sensors.getTemperatureK(ADC_ALTERNATOR_NTC2, false),1.0, 273.15, ",");
      Serial.print(" erT=");
      printN2K(sensors.getTemperatureK(ADC_ENGINEROOM_NTC3, false),1.0, 273.15);
    }
  }
}


void(* resetDevice) (void) = 0; //declare reset function @ address 0

void setEngineHours() {
  Serial.setTimeout(10000);
  Serial.print(F("Engine Hours ?>"));
  char buffer[10];
  size_t l = Serial.readBytesUntil('\n', buffer, 9);
  if ( l > 0) {
    buffer[l] = '\0';
    double hours = atof(buffer);
    Serial.print(F("Engine Hours:"));
    Serial.println(hours);
    sensors.setEngineSeconds(hours*3600.0);
  } else {
    Serial.println("");
    Serial.println(F("canceled"));
  }
  Serial.setTimeout(100);
}

void setStoredVddVoltage() {
  Serial.setTimeout(10000);
  Serial.print(F("Vdd Voltage ?>"));
  char buffer[10];
  size_t l = Serial.readBytesUntil('\n', buffer, 9);
  if ( l > 0) {
    buffer[l] = '\0';
    double measuredVoltagee = atof(buffer);
    Serial.print(F("Vdd Voltage:"));
    Serial.println(measuredVoltagee,5);
    sensors.setStoredVddVoltage(measuredVoltagee);
  } else {
    Serial.println("");
    Serial.println(F("canceled"));
  }
  Serial.setTimeout(100);
}

void toggleDiagnostics() {
  static bool diagnostics = false;
  diagnostics = !diagnostics;
  engineMonitor.setDiagnostics(diagnostics);
}

void showHelp() {
  Serial.println(F("N2K Engine monitor."));
  Serial.print(F("Git Version: "));Serial.println(F(GIT_SHA1_VERSION));
  Serial.println(F("  - Send 'h' help"));
  Serial.println(F("  - Send 'E' set hours"));
  Serial.println(F("  - Send 'V' set Vdd "));
  Serial.println(F("  - Send 'F' fake Engine RPM at 1K"));
  Serial.println(F("  - Send 's' status"));
  Serial.println(F("  - Send 'C' clear events"));
  Serial.println(F("  - Send 'd' toggle N2k debug"));
  Serial.println(F("  - Send 'D' toggle Sensor debug"));
  Serial.println(F("  - Send 'M' toggle Engine debug"));
  Serial.println(F("  - Send 'R' restart"));
}




void checkCommand() {
  // Remove after testing
  static uint8_t eventId = 1;
  if (Serial.available()) {
    char chr = Serial.read();
    switch ( chr ) {
      case 'h': showHelp(); break;
      case 's':
        showStatus();
        break;
      case 'E':
        setEngineHours();
        break;
      case 'e':
        // NOT in the menu, only here for testing
        sensors.localStorage.engineHoursPeriods += 10;
        sensors.localStorage.saveEvent(eventId++);
        break;
      case 'F':
        sensors.toggleFakeEngineRunning();
        break;
      case 'd':
        toggleDiagnostics();
        break;
      case 'D':
        sensorDebug = !sensorDebug;
        break;
      case 'M':
        monitorEnabled = !monitorEnabled;
        break;
      case 'C':
        sensors.localStorage.clearEvents();
        break;
      case 'V':
        setStoredVddVoltage();
        break;
      case 'R':
        Serial.println(F("Restart"));
        delay(100);
        resetDevice();
        break;
    }
  }
}




void messageHandler(MessageHeader *requestMessageHeader, byte * buffer, int len) {
  if ( requestMessageHeader->pgn == ENGINE_PROPRIETARY_PGN) { // single packet pro[prietary]

    uint16_t id = (((unsigned long )buffer[2])<<16)|(((unsigned long )buffer[1])<<8)|(buffer[0]);
    if ( id == ENGINE_PROPRIETARY_CODE ) { // matches us 2046 + marine industry
      uint8_t function = buffer[2];
      if ( function == FN_DUMP_EVENTS) { // a function we recognise, dump the stored events
        // requested error history
        uint8_t nevents = sensors.localStorage.countEvents();
        MessageHeader messageHeader(ENGINE_PROPRIETARY_FP_PGN, 6, engineMonitor.getAddress(), requestMessageHeader->source);
        engineMonitor.startFastPacket(&messageHeader, 2+2+4+nevents*4);
        engineMonitor.output2ByteUInt(ENGINE_PROPRIETARY_CODE);
        engineMonitor.outputByte(FN_DUMP_EVENTS_RESP);
        engineMonitor.outputByte(nevents+1);
        engineMonitor.outputByte(0);
        double h = 0.004166666667*sensors.localStorage.engineHoursPeriods;
        engineMonitor.output3ByteUDouble(h, 0.001);
        uint32_t lastEvent = 0;
        for(int i = 0; i < nevents; i++) {
          uint8_t eventId = sensors.localStorage.nextEvent(lastEvent);
          engineMonitor.outputByte(eventId);
          h = 0.004166666667*lastEvent;
          engineMonitor.output3ByteUDouble(h, 0.001);
        }
        engineMonitor.finishFastPacket();
      } else if ( function == FN_CLEAR_EVENTS) { // clear stored events
        sensors.localStorage.clearEvents();
        MessageHeader messageHeader(ENGINE_PROPRIETARY_PGN, 6, engineMonitor.getAddress(), requestMessageHeader->source);
        engineMonitor.startPacket(&messageHeader);
        engineMonitor.output2ByteUInt(ENGINE_PROPRIETARY_CODE);
        engineMonitor.outputByte(FN_CLEAR_EVENTS_RESP);
        engineMonitor.finishPacket();
      } 
      // TODO, consider replacing serial functions with CAN proprietary messages 
      // which are easier to send without direct access to the serial port.
      // setEngineHours - no real point in exposing this over can
      // setStoredVddVoltage -- the reading for this is only available with the box open and should never change. 

    }
  }
}


void setup() {
  Serial.begin(19200);
  Serial.println(F("Luna engine monitor start"));
  setupLed();
  engineMonitor.setMessageHandler(messageHandler);
  Serial.println(F("Opening CAN"));
#ifdef CANCONTROLLER_SPEED_8MHZ
  while (!engineMonitor.open(MCP_8MHz) ) {
#else
  while (!engineMonitor.open(MCP_16MHz) ) {
#endif
    Serial.println(F("CAN Failed"));
    delay(5000);
    blinkLed(2);
  }
  Serial.println(F("Opened, MCP2515 Operational"));

  while(!sensors.begin() ) {
    Serial.println(F("Engine Sensors failed"));
    delay(5000);
    blinkLed(3);
  }

#ifndef INSPECT_FLASH_USAGE
  Serial.print(F("Starting one wire on:"));
  Serial.println(PIN_ONE_WIRE);
  oneWire.begin();
  Serial.println(F("Sarting sensor"));
  oneWireSensor.begin();
#endif
  blinkLed(4);

  Serial.println(F("Running..."));;
}

void loop() {
  sensors.read(sensorDebug);
  asyncBlink();
  monitor();
#ifndef INSPECT_FLASH_USAGE  
  oneWireSensor.readOneWire();
#endif
  sendRapidEngineData();
  sendEngineData();
  sendVoltages();
  sendTemperatures();
  sendFuel();
  engineMonitor.processMessages();
  checkCommand();
}

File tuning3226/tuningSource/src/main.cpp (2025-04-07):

#include <Arduino.h>
#include "parts.h"
#include <util/delay.h>
#include <EEPROM.h>
// *INDENT-OFF*  this code is unreadable of you follow astyle's conventions!
//#if __AVR_ARCH__ >=100
/* FOR MODERN AVRs:
 *
 *  tinyAVR must use PB0, PB1 or PB2 (PB2 is by default a serial pin though.
 *  In order for these to be good tuning sources you must have an external clock chip on them, or have a watch crystal connected to them and use RTC tuning mode.
 *  Same goes for AVR DA and megaAVR 0-series.
 *
 *  AVR DB-series and DD-series parts can use a simple MHz crystal.
 *
 *  Your tuning will never be better than the thing you're tuning it from, so don't use something
 *  running on an internal oscillator - just grab any pro mini clone which you can see the HC/49 16 mhz crystal on (the tiny ones are often much less accurate
 *  ceramic resonators that are barely better than the modern internal oscillator. )
 */
#ifndef TUNE_OUTPUT_PIN // If not defined in parts.h, need to pick default pin
  #ifndef TUNE_WITH_RTC // First the non-RTC version
    #if !defined(MEGATINYCORE)
      #if (_AVR_PINCOUNT > 14)
        // Except under tight constraints of 14-pin non-tinies, we can always count on their being a PA2.
        #define TUNE_OUTPUT_PIN PIN_PA2
      #elif defined(PIN_PC2) /*AVR DD-series has no PC0, PA2-7, and the only pins nubered 2 or lower in any port
        * are thus PA0, PA1, and PC1 and PC2. The pins on PORTA are needed for the crystal if this is to be used
        * and you actually want to tune to within an accuracy measured in  (tens of) "ppm" instead of  (several) "%" on datasheet specs.
        * So we're using either PC1 or PC2!
        */
        #define TUNE_OUTPUT_PIN PIN_PC2
     /* This must be a pin that exists, and which is numbered 0-2 in the port; we will use TCA0 to
      * generate it and set PORTMUX.TCAROUTEA appropriately.
      * This sketch uses TCA0 to generate the tuning signal, and hence you can't use it for millis
      * Well - you can, and it will still tune parts perfectly well, but only because we don't rely on
      * millis in any way shape or form to get our timing (if we did it'[d be totally fucked_/
      *
      * This sketch does not support using the CCL to redirect these orphaned output channels to usable pins,
      * and this is in fact practically trivial to do without even using the libraries.
      */
      #endif
    #else /* tinyAVR */
      #define TUNE_OUTPUT_PIN PIN_PB0 /* pins B1 and B2 also work. No other pins are supported. */
    #endif
  #else
    #if (defined(MEGATINYCORE) || !defined(DD_14_PINS))
      #define TUNE_OUTPUT_PIN PIN_PA2
    #else
      #define TUNE_OUTPUT_PIN PIN_PD7
    #endif
  #endif
#else // TUNE_OUTPUT_PIN defined
  #ifndef TUNE_WITH_RTC
    #if !((((defined(PIN_PA0) && TUNE_OUTPUT_PIN == PIN_PA0) || (defined(PIN_PA1) && TUNE_OUTPUT_PIN == PIN_PA1) ||  (defined(PIN_PA2) && TUNE_OUTPUT_PIN == PIN_PA2)  || \
            (defined(PIN_PC0) && TUNE_OUTPUT_PIN == PIN_PC0) || (defined(PIN_PC1) && TUNE_OUTPUT_PIN == PIN_PC1) ||  (defined(PIN_PC2) && TUNE_OUTPUT_PIN == PIN_PC2)  || \
            (defined(PIN_PD1) && TUNE_OUTPUT_PIN == PIN_PD1) || (defined(PIN_PD2) && TUNE_OUTPUT_PIN == PIN_PD2) ||  (defined(PIN_PD0) && TUNE_OUTPUT_PIN == PIN_PD0)  || \
            (defined(PIN_PE0) && TUNE_OUTPUT_PIN == PIN_PE0) || (defined(PIN_PE1) && TUNE_OUTPUT_PIN == PIN_PE1) ||  (defined(PIN_PE2) && TUNE_OUTPUT_PIN == PIN_PE2)  || \
            (defined(PIN_PF0) && TUNE_OUTPUT_PIN == PIN_PF0) || (defined(PIN_PF1) && TUNE_OUTPUT_PIN == PIN_PF1) ||  (defined(PIN_PF2) && TUNE_OUTPUT_PIN == PIN_PF2)  || \
            (defined(PIN_PG0) && TUNE_OUTPUT_PIN == PIN_PG0) || (defined(PIN_PG1) && TUNE_OUTPUT_PIN == PIN_PG1) ||  (defined(PIN_PG2) && TUNE_OUTPUT_PIN == PIN_PG2)) || \
           ((defined(PIN_PB0) && TUNE_OUTPUT_PIN == PIN_PB0) || (defined(PIN_PB1) && TUNE_OUTPUT_PIN == PIN_PB1) ||  (defined(PIN_PB2) && TUNE_OUTPUT_PIN == PIN_PB2)))
      #error "Invalid or unusable custom output pin defined"
    #endif
  #else // TUNE_WITH_RTC
    #if (defined(MEGATINYCORE) && MEGATINYCORE_SERIES < 2)
      #if  (!((defined(PIN_PA2) && TUNE_OUTPUT_PIN == PIN_PA2) || (defined(PIN_PB2) && TUNE_OUTPUT_PIN == PIN_PB2) || (defined(PIN_PC2) && TUNE_OUTPUT_PIN == PIN_PC2)))
        #error "Cannot use RTC derved tuning signal on this pin"
      #endif
    #else
      #if (!((defined(PIN_PA2) && TUNE_OUTPUT_PIN == PIN_PA2) || (defined(PIN_PA7) && TUNE_OUTPUT_PIN == PIN_PA7) || \
             (defined(PIN_PB2) && TUNE_OUTPUT_PIN == PIN_PB2) || (defined(PIN_PB7) && TUNE_OUTPUT_PIN == PIN_PB7) || \
             (defined(PIN_PC2) && TUNE_OUTPUT_PIN == PIN_PC2) || (defined(PIN_PC7) && TUNE_OUTPUT_PIN == PIN_PC7) || \
             (defined(PIN_PD2) && TUNE_OUTPUT_PIN == PIN_PD2) || (defined(PIN_PD7) && TUNE_OUTPUT_PIN == PIN_PD7) || \
             (defined(PIN_PE2) && TUNE_OUTPUT_PIN == PIN_PE2) || (defined(PIN_PE7) && TUNE_OUTPUT_PIN == PIN_PE7) || \
             (defined(PIN_PF2) && TUNE_OUTPUT_PIN == PIN_PF2) || (defined(PIN_PF7) && TUNE_OUTPUT_PIN == PIN_PF7) || \
             (defined(PIN_PG2) && TUNE_OUTPUT_PIN == PIN_PG2) || (defined(PIN_PG7) && TUNE_OUTPUT_PIN == PIN_PG7)))
        #error "cannout use RTC derived tuning signal on this pin."
      #endif
    #endif
  #endif // end check tuning pins
#endif // end tuning pin select or check.
/* FOR CLASSIC AVRs:
 *  Uncomment which comopare channel you wish to enable (sorry not done by pins here...
 *  default will come out pin 9 on a 328p or 328pb... Hell you can even use an MHET Micronucleus t88.
 *  Anything with a 16-bit timer and a crystal or external clock
 */
#if (TIMER1_TYPICAL == 87)
  CONFIGURE_PWM();
  #define ENABLEOC1A 0
  #define ENABLEOC1B 1
#else
  #define ENABLEOC1A 1
  #define ENABLEOC1B 0
#endif
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

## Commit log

2024-12-01 Created board and loaded bootloader
    [atmel328pBoard.kicad_pcb, atmel328pBoard.kicad_sch]
2024-12-02 Ported code and adjusted to new pcb
2024-12-04 reading sensors on demand where possible
2024-12-10 Added oil pressure and status, modified pcb
    [atmel328pBoard.kicad_pcb, atmel328pBoard.kicad_sch]
2024-12-17 Added screenshots and case
    [case.scad, case.stl, lid.stl]
2025-01-06 Added a attiny3226 veresion for better ADC accuracy
    [attiny3226Board.kicad_pcb, attiny3226Board.kicad_sch]
2025-01-11 Corrected output to latest version
    [main2.cpp]
2025-01-11 Bisected and Fixed.
    Detail. If EEPROM is witten to continuously it will mess with ISRs
    on a attiny and cause millis and micros to not be stable.
    But was introduced by refactoring the storage of engine hours.
    Now need to check that the 328p code is not in the same state on
    the device where it was flashed as that could break the EEPROM
    on the chip.
    [main.cpp]
2025-01-19 Finally mare the RPM to pulse amp stable
    [atmel328pBoard.kicad_pcb, atmel328pBoard.kicad_sch, attiny3226Board.kicad_pcb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]
2025-04-07 Improved flywheel detection circuit
    [attiny3226Board.kicad_pcb, attiny3226Board.kicad_sch, case.stl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]
2025-04-13 Added protection for ovre voltages on measurements
    [attiny3226Board.kicad_pcb, attiny3226Board.kicad_sch]
2025-05-11 Fixed startup and hopefully shutdown alarms
    [main.cpp]
2025-06-24 Improvd ADC stability
    [attiny3226Board.kicad_pcb, attiny3226Board.kicad_sch]
2025-06-27 Added the current engine hours to PGN130817
2025-07-06 Fixed Onewire on Attiny3226
    [main.cpp]
2025-07-08 Fixed n events and added read stop solenoid
    [main.cpp]
2025-07-22 Fixed spurious alarms
    [attiny3226Board.kicad_sch]
2026-06-22 Attempt to make the coolant temperature more stable
2026-06-28 Exhaust temp sensor is mounted on the wet exhaust silencer body, not the elbow
2026-06-28 Improved voltage sampling
    [attiny3226Board.kicad_sch]
